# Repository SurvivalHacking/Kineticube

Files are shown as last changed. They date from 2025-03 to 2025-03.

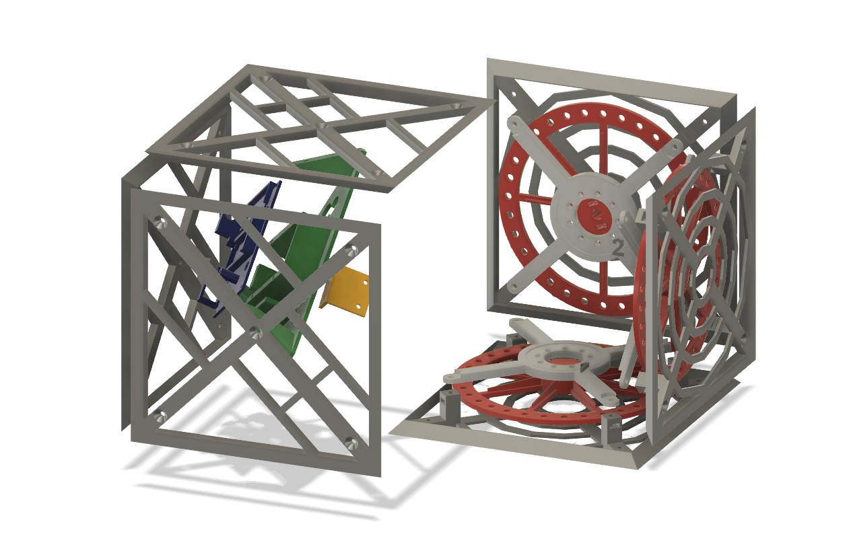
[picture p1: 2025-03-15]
Global Assembly.jpg

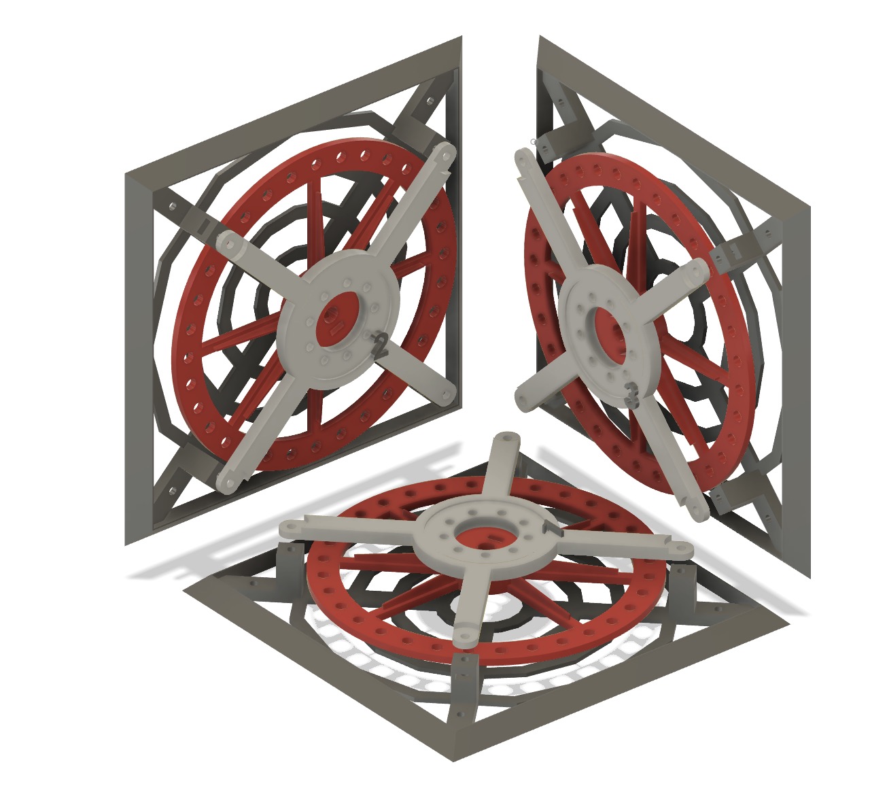
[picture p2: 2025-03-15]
Motor sequence.jpg

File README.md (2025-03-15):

Sometimes the futile things are always the most fascinating. 
Today I present the realisation of this self-balancing cube, nemed KinetiCube. 
An hypnotic cube that concentrates several scientific disciplines within it: Physics, mechanics, electronics and mathematics. 
As in an orchestra all working together in concert to make this cube stand upright.
Despite its simplicity, numerous operations and calculations are carried out in order to establish the right forces to be deployed. 
A beauty to look at and why not an opportunity to learn a few things from many angles. Sometimes even a simple game can become important for our growth. 
An open source project, which was, however, complex to realise and calibrate, so I put my own spin on it to make it feasible for everyone.

In addition I also made for a friend, the magician HYDE a version resembling a rubik's cube.
In this version, a number of improvements have been made to make it even simpler and aesthetically beautiful

Full video tutorial: https://youtu.be/8I2puoh9CxE 

EPXX-kineticube

COVER

Electronic assembly

Motor sequence

Global Assembly

Screenshot 2025-03-15 alle 20 30 26

Screenshot 2025-03-14 alle 22 32 57

Screenshot 2025-03-15 alle 20 29 16

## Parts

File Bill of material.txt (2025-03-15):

Tutorial video: https://youtu.be/8I2puoh9CxE

Bill of Material
🎛️ Nidec Motor 24H - ALI: https://s.click.aliexpress.com/e/_oEclh0V
🎛️ Digital Buzzer - ALI: https://s.click.aliexpress.com/e/_ooe48Gv
🎛 7mm Push Button - ALI: https://s.click.aliexpress.com/e/_Dnebs3t
🎛️ Power Switch 10x15 ALI: https://s.click.aliexpress.com/e/_DkAxjLh
🎛 Arduino Nano ALI: https://s.click.aliexpress.com/e/_DdZQhcR
🎛 Battery 11.1V 650mA - ALI: https://s.click.aliexpress.com/e/_omINxTT
🎛 XT30 battery cable - ALI: https://s.click.aliexpress.com/e/_ooCZeMv
🎛 Bluetooth Module HC05 - ALI: https://s.click.aliexpress.com/e/_oEKJG53

Original project:
https://github.com/remrc/Self-Balancing-Cube
https://hackaday.io/project/198415-arduino-3d-printed-self-balancing-cube

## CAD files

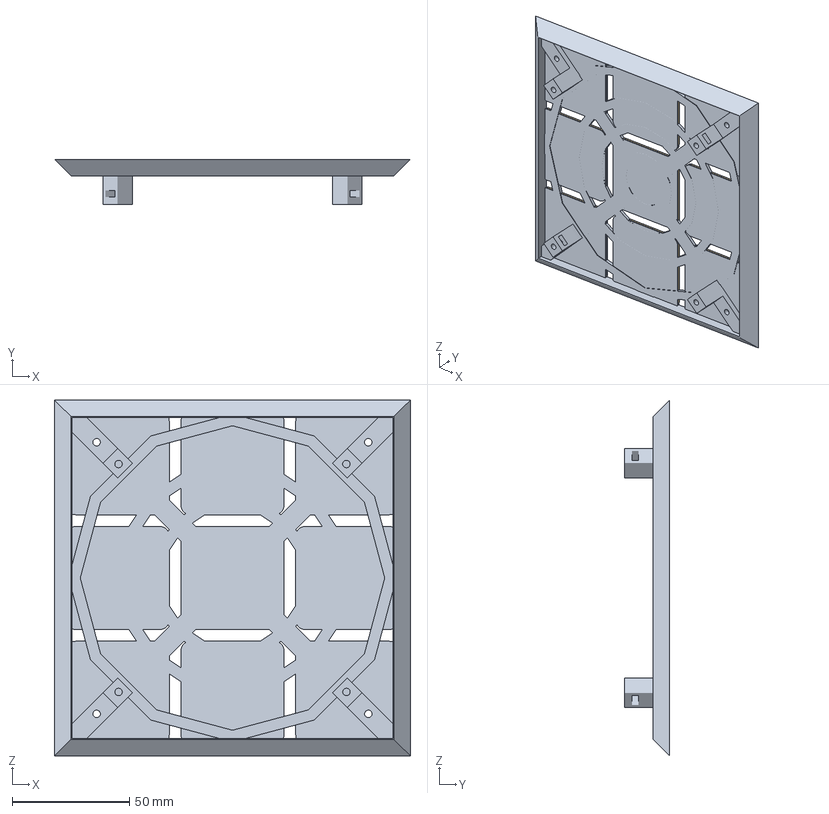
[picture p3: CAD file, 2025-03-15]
3D-HYDE/Motor Side.3mf
152.0 x 19.3 x 152.0 mm
Scheletro (4)
Sticker 1 (2) (2) (2) (2) (1) (1) (1)
Sticker 1 (2) (2) (2) (2) (1) (1) (2) (1)
Sticker 1 (2) (2) (2) (2) (1) (1) (2) (2)
Sticker 1 (2) (2) (2) (2) (1) (1) (2) (3)
Sticker 1 (2) (2) (2) (2) (1) (1) (2) (4)
Sticker 1 (2) (2) (2) (2) (1) (1) (2) (5)
Sticker 1 (2) (2) (2) (2) (1) (1) (2)
Sticker 1 (2) (2) (2) (2) (1) (1) (3)
Sticker 1 (2) (2) (2) (2) (1) (1)

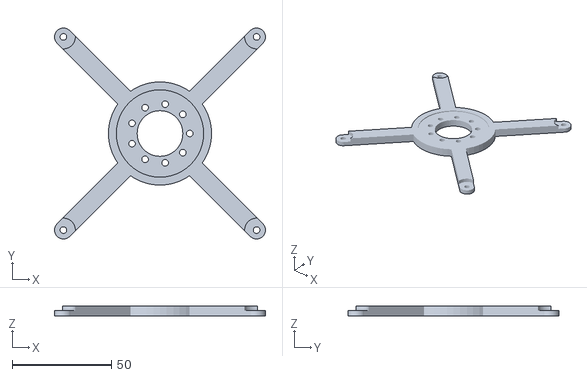
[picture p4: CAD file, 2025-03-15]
3D/Motor Support X3.stl
106.3 x 106.3 x 5.00

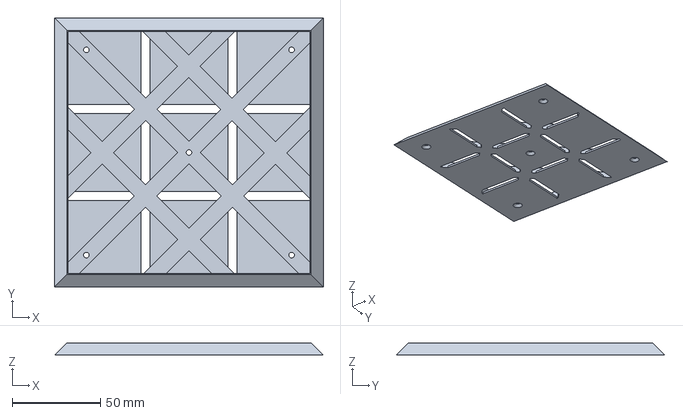
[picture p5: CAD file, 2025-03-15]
3D-HYDE/Normal side 2- BAMBULAB.3mf
152.0 x 152.0 x 7.00 mm

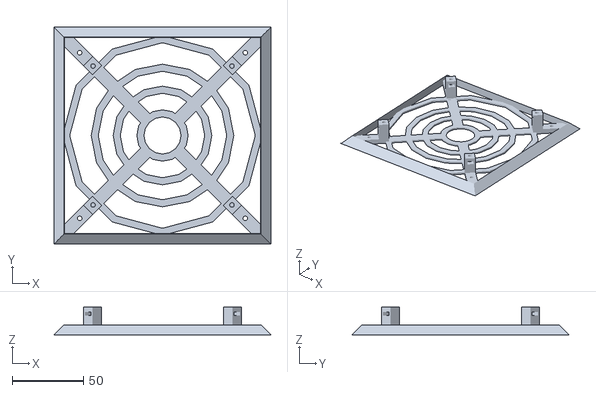
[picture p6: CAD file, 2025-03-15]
3D/Motor Side X3.stl
152.0 x 152.0 x 19.3

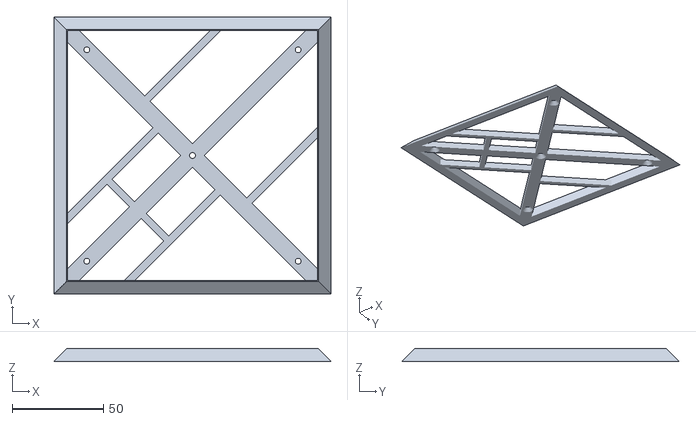
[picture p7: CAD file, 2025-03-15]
3D/Normal Side X3.stl
152.0 x 152.0 x 7.00

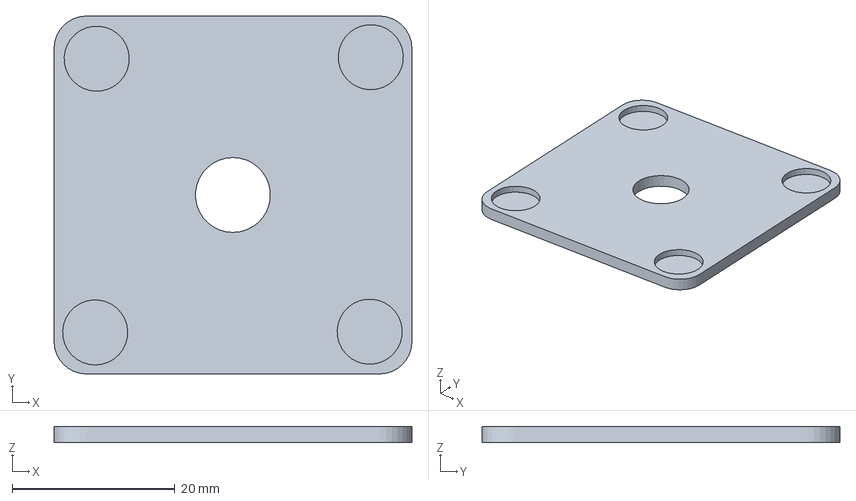
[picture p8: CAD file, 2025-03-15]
3D-HYDE/Magnet Sticker - BAMBULAB.3mf
44.0 x 44.0 x 2.00 mm

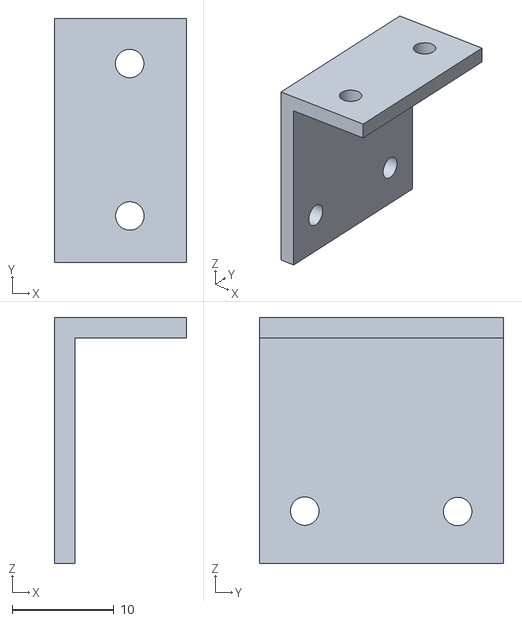
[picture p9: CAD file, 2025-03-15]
3D/Gyro Support.stl
13.0 x 24.1 x 24.2

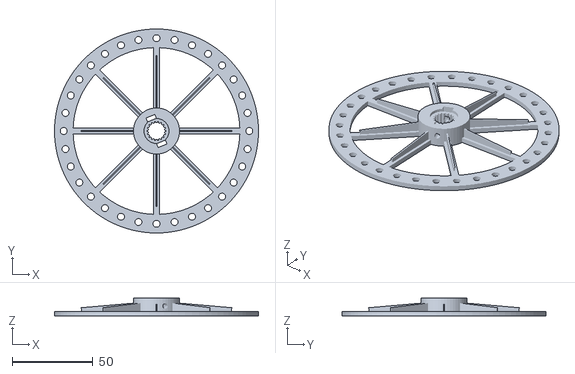
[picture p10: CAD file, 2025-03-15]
3D/Wheel 8mm hole X3.stl
126.4 x 126.4 x 11.0

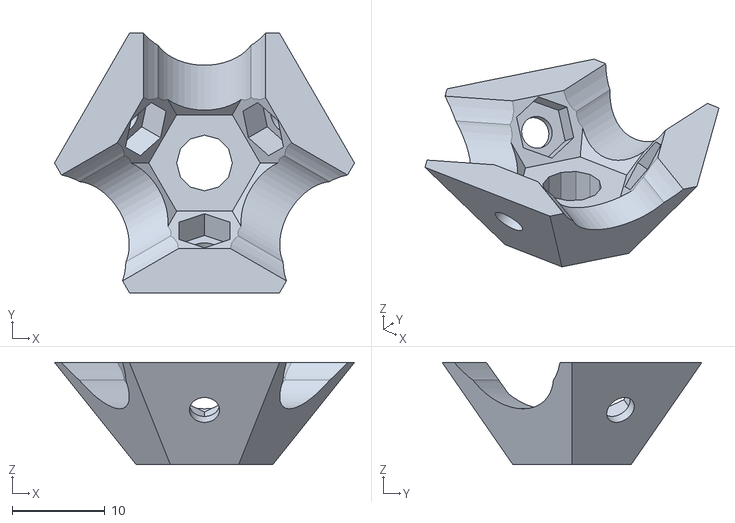
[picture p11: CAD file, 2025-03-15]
3D/Corners 8x.stl
32.3 x 28.0 x 11.0

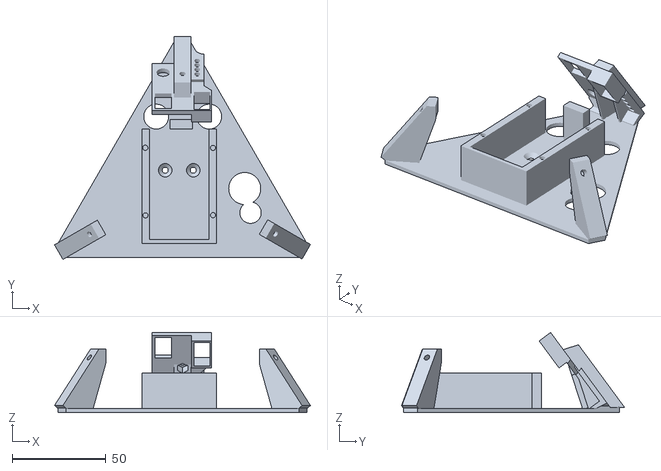
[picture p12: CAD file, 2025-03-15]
3D-HYDE/Electronic Support.stl
136.6 x 119.0 x 42.7

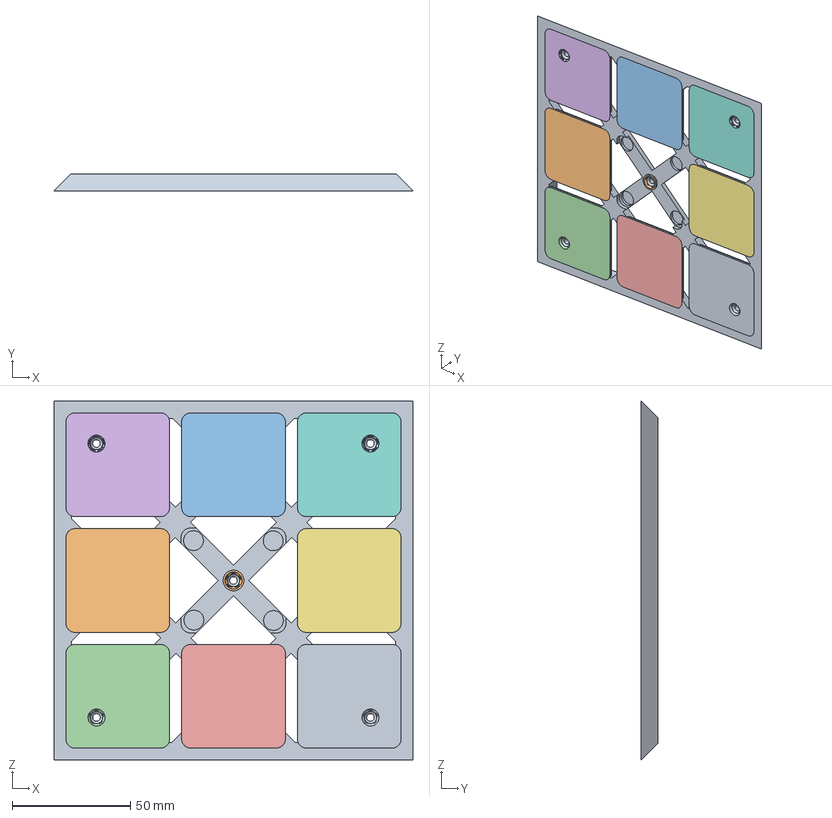
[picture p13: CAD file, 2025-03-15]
3D-HYDE/Normal Side magnet.3mf
152.0 x 7.00 x 152.0 mm
Scheletro (3) (1)
Sticker 1 (3) (3) (1) (1) (1)
Sticker 1 (3) (3) (1) (2) (1)
Sticker 1 (3) (3) (1) (3) (1)
Sticker 1 (3) (3) (1) (4) (1)
Sticker 1 (3) (3) (1) (5) (1)
Sticker 1 (3) (3) (1) (6) (1)
Sticker 1 (3) (3) (1) (7) (1)
Sticker 1 (3) (3) (1) (8)
Sticker 1 (3) (3) (2)

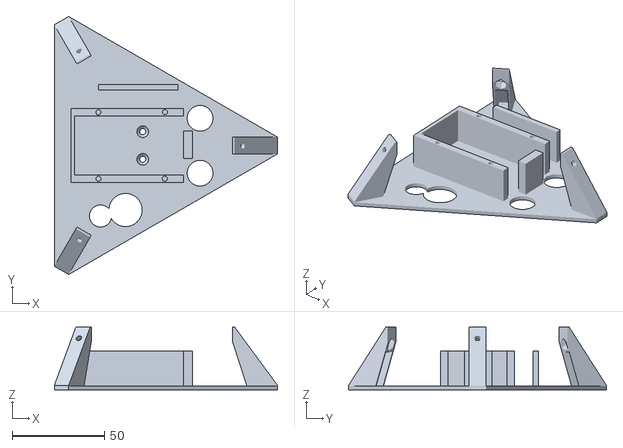
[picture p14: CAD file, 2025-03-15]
3D/Central Support.stl
121.2 x 139.9 x 34.1

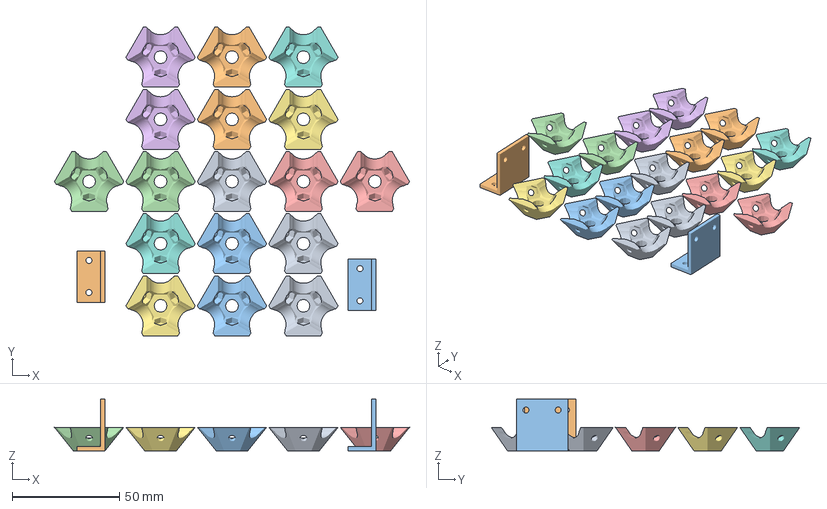
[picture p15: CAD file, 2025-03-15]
3D-HYDE/Internal and gyro FIX.3mf
165.6 x 143.9 x 24.2 mm
Corners 8x.stl x 17
Gyro Support.stl x 2

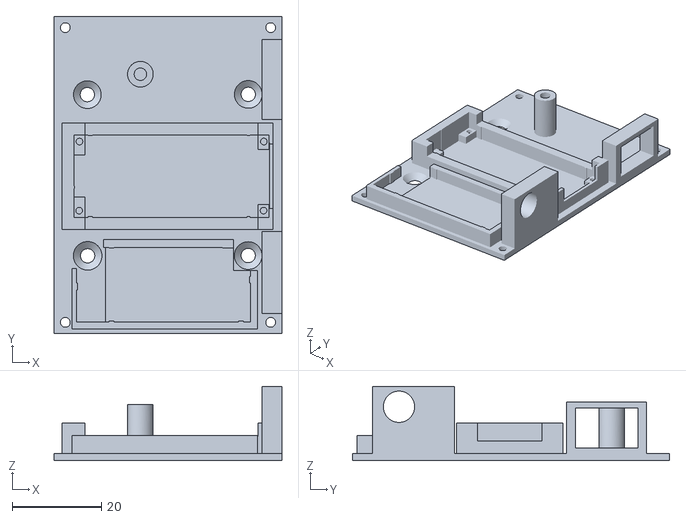
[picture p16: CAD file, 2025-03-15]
3D/Electronic Support.stl
51.0 x 71.0 x 16.6

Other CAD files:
3D-HYDE/Normal side 1- BAMBULAB.3mf
3D-HYDE/Motor Side 1- BAMBULAB.3mf
3D-HYDE/Normal Side.3mf
3D/Wheel 6mm hole X3.stl
3D-HYDE/Magnet sticker.3mf
3D-HYDE/Motor Side 2- BAMBULAB.3mf
3D-HYDE/Motor Support.3mf
3D-HYDE/Normal side 3 mgnet- BAMBULAB.3mf

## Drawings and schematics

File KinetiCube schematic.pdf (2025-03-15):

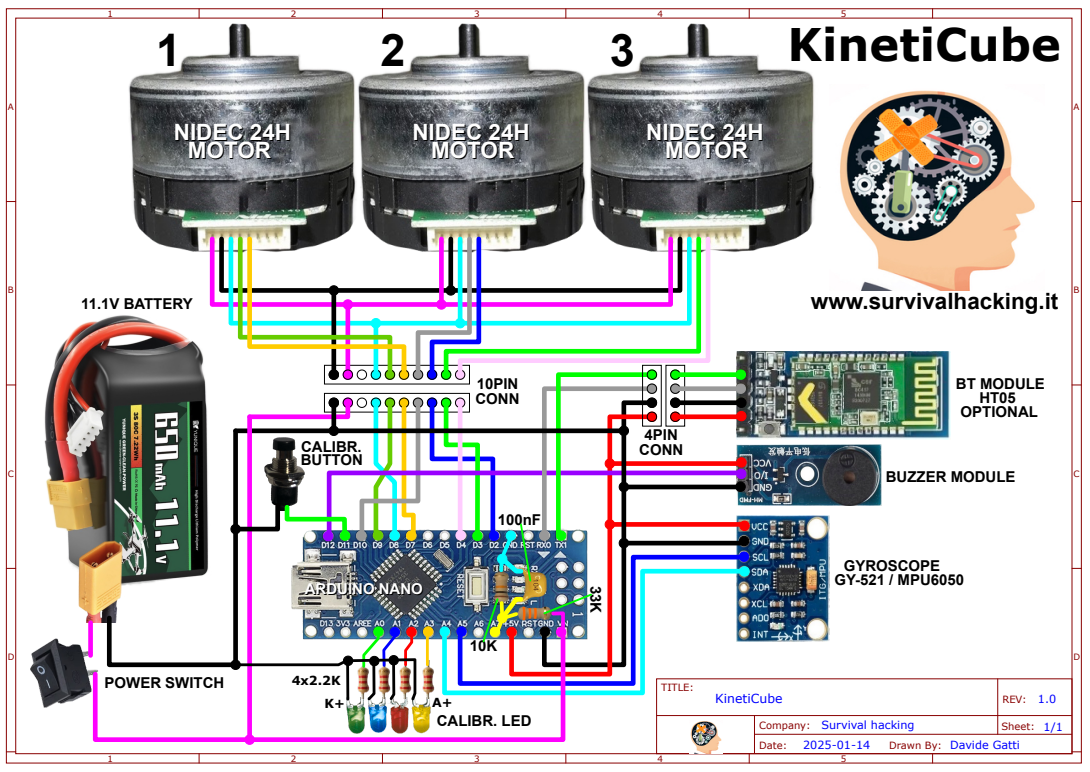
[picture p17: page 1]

CALIBR. BUTTON

TITLE:

KinetiCube | REV: 1.0

Company: Survival hacking | Sheet: 1/1

Drawn By: Davide Gatti

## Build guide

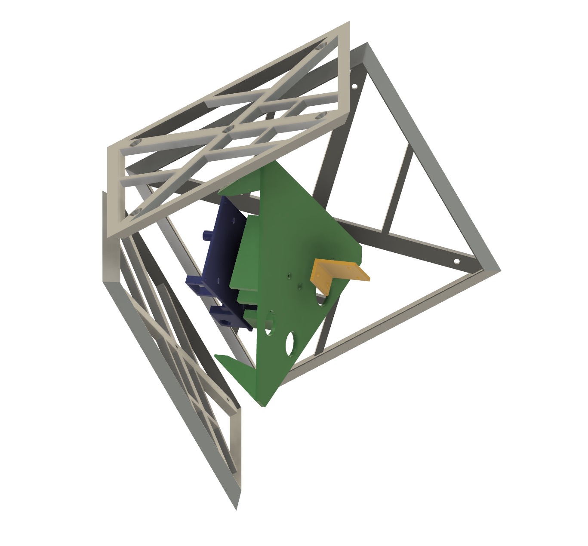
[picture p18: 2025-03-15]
Electronic assembly.jpg

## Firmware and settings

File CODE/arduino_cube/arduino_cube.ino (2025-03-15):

// Modified 20/01/2025 by Davide Gatti (www.survivalhacking.it) 
// Added manual calibration via pushbutton
// Added 4 LED for show calibration status

// Press  button to start calibration, press again to store calibration point (repeat the fo three edges and one angle
// If press button during power-up, forget current calibration


#include "arduino_cube.h"
#include <Wire.h>
#include <EEPROM.h>

void setup() {
  Serial.begin(115200);

  TCCR1A = 0b00000001;
  TCCR1B = 0b00001010;
  TCCR2B = 0b00000010;
  TCCR2A = 0b00000011;

  pinMode(DIR_1, OUTPUT);
  pinMode(DIR_2, OUTPUT);
  pinMode(DIR_3, OUTPUT);
  pinMode(BRAKE, OUTPUT);
  pinMode(BUZZER, OUTPUT);
  pinMode(CALIBRATE, INPUT_PULLUP);
  pinMode(LED_1, OUTPUT);
  pinMode(LED_2, OUTPUT);
  pinMode(LED_3, OUTPUT);
  pinMode(LED_4, OUTPUT);

  Motor1_control(0);
  Motor2_control(0);
  Motor3_control(0);
  if  (!digitalRead(CALIBRATE)) { // if press button during power on reset calibration
    save();
    beep();
    beep();
    beep();
  }
  
  EEPROM.get(0, offsets);
  if (offsets.ID1 == 99 && offsets.ID2 == 99 && offsets.ID3 == 99 && offsets.ID4 == 99) {
    calibrated = true;
  }else{
    calibrated = false;
  }
  
  Update_calibrated_LED();

  delay(3000);
  beep();
  angle_setup();
}

void loop() {

  currentT = millis();

  if (currentT - previousT_1 >= loop_time) {
    Tuning();  // derinimui
    angle_calc();
    
    if (balancing_point == 1) {
      angleX -= offsets.X1;
      angleY -= offsets.Y1;
      if (abs(angleX) > 8 || abs(angleY) > 8) vertical = false;
    } else if (balancing_point == 2) {
      angleX -= offsets.X2;
      angleY -= offsets.Y2;
      if (abs(angleY) > 6) vertical = false;
    } else if (balancing_point == 3) {
      angleX -= offsets.X3;
      angleY -= offsets.Y3;
      if (abs(angleY) > 6) vertical = false;
    } else if (balancing_point == 4) {
      angleX -= offsets.X4;
      angleY -= offsets.Y4;
      if (abs(angleX) > 6) vertical = false;
    }
 
    if (vertical && calibrated && !calibrating) {    
      digitalWrite(BRAKE, HIGH);
      gyroZ = GyZ / 131.0; // Convert to deg/s
      gyroY = GyY / 131.0; // Convert to deg/s

      gyroYfilt = alpha * gyroY + (1 - alpha) * gyroYfilt;
      gyroZfilt = alpha * gyroZ + (1 - alpha) * gyroZfilt;
      
      int pwm_X = constrain(pGain * angleX + iGain * gyroZfilt + sGain * motor_speed_pwmX, -255, 255); // LQR
      int pwm_Y = constrain(pGain * angleY + iGain * gyroYfilt + sGain * motor_speed_pwmY, -255, 255); // LQR
      motor_speed_pwmX += pwm_X; 
      motor_speed_pwmY += pwm_Y;
      
      if (balancing_point == 1) {
        XY_to_threeWay(-pwm_X, -pwm_Y);
      } else if (balancing_point == 2) {
        Motor1_control(-pwm_Y);
      } else if (balancing_point == 3) {
        Motor2_control(pwm_Y);
      } else if (balancing_point == 4) {
        Motor3_control(-pwm_X);
      }
    } else {
      balancing_point = 0;
      XY_to_threeWay(0, 0);
      digitalWrite(BRAKE, LOW);
      motor_speed_pwmX = 0;
      motor_speed_pwmY = 0;
    }
    previousT_1 = currentT;
  }
  
  if (currentT - previousT_2 >= 2000) {    
    battVoltage((double)analogRead(VBAT) / bat_divider); 
    if (!calibrated && !calibrating) {
      Serial.println("first you need to calibrate the balancing points...");
    }
    previousT_2 = currentT;
  }
}

void Update_calibrated_LED() {
  EEPROM.get(0, offsets);
  digitalWrite(LED_1, LOW);
  digitalWrite(LED_2, LOW);
  digitalWrite(LED_3, LOW);
  digitalWrite(LED_4, LOW);
  if (offsets.ID1 == 99) {
    digitalWrite(LED_1, HIGH);
  }
  if (offsets.ID2 == 99) {
    digitalWrite(LED_2, HIGH);
  }
  if (offsets.ID3 == 99) {
    digitalWrite(LED_3, HIGH);
  }
  if (offsets.ID4 == 99) {
    digitalWrite(LED_4, HIGH);
  }
}

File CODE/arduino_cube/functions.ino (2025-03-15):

void writeTo(byte device, byte address, byte value) {
  Wire.beginTransmission(device);
  Wire.write(address);
  Wire.write(value);
  Wire.endTransmission(true);
}

void beep() {
    digitalWrite(BUZZER, HIGH);
    delay(70);
    digitalWrite(BUZZER, LOW);
    delay(80);
}

void save() {
    EEPROM.put(0, offsets);
    EEPROM.get(0, offsets);
    if (offsets.ID1 == 99 && offsets.ID2 == 99 && offsets.ID3 == 99 && offsets.ID4 == 99) { 
      calibrated = true;
      tone(BUZZER, 1000, 500);
      tone(BUZZER, 2000, 500);
      tone(BUZZER, 3000, 500);
      tone(BUZZER, 4000, 500);
      tone(BUZZER, 5000, 500);
    }else{
      calibrating = false;
    }
    Update_calibrated_LED();
    Serial.println("calibrating off");
    beep();
}

void angle_setup() {
  Wire.begin();
  delay (100);
  writeTo(MPU6050, PWR_MGMT_1, 0);
  writeTo(MPU6050, ACCEL_CONFIG, accSens << 3); // Specifying output scaling of accelerometer
  writeTo(MPU6050, GYRO_CONFIG, gyroSens << 3); // Specifying output scaling of gyroscope
  delay (100);

  for (int i = 0; i < 1024; i++) {
    angle_calc();
    //Serial.println(GyZ);
    GyZ_offset_sum += GyZ;
    delay(3);
  }
  GyZ_offset = GyZ_offset_sum >> 10;
  Serial.print("GyZ offset value = "); Serial.println(GyZ_offset);
  beep();
  
  for (int i = 0; i < 1024; i++) {
    angle_calc();
    //Serial.println(GyY);
    GyY_offset_sum += GyY;
    delay(3);
  }
  GyY_offset = GyY_offset_sum >> 10;
  Serial.print("GyY offset value = "); Serial.println(GyY_offset);
  beep();
  beep();
}

void angle_calc() {
  
  // read raw accel/gyro measurements from device
  Wire.beginTransmission(MPU6050);
  Wire.write(0x45);
  Wire.endTransmission(false);
  Wire.requestFrom(MPU6050, 6, true);  
  GyY = Wire.read() << 8 | Wire.read(); // 0x45 (GYRO_YOUT_H) & 0x46 (GYRO_YOUT_L)
  GyZ = Wire.read() << 8 | Wire.read(); // 0x47 (GYRO_ZOUT_H) & 0x48 (GYRO_ZOUT_L)

  Wire.beginTransmission(MPU6050);
  Wire.write(0x3B);                  
  Wire.endTransmission(false);
  Wire.requestFrom(MPU6050, 6, true);  
  AcX = Wire.read() << 8 | Wire.read(); // 0x3B (ACCEL_XOUT_H) & 0x3C (ACCEL_XOUT_L)
  AcY = Wire.read() << 8 | Wire.read(); // 0x3D (ACCEL_YOUT_H) & 0x3E (ACCEL_YOUT_L)
  AcZ = Wire.read() << 8 | Wire.read(); // 0x3F (ACCEL_ZOUT_H) & 0x40 (ACCEL_ZOUT_L)

  GyZ -= GyZ_offset;
  GyY -= GyY_offset;

  robot_angleX += GyZ * loop_time / 1000 / 65.536;
  Acc_angleX = atan2(AcY, -AcX) * 57.2958;
  robot_angleX = robot_angleX * Gyro_amount + Acc_angleX * (1.0 - Gyro_amount);

  robot_angleY += GyY * loop_time / 1000 / 65.536;
  Acc_angleY = -atan2(AcZ, -AcX) * 57.2958; 
  robot_angleY = robot_angleY * Gyro_amount + Acc_angleY * (1.0 - Gyro_amount);

  angleX = robot_angleX;
  angleY = robot_angleY;

  if (abs(angleX - offsets.X1) < 0.4 && abs(angleY - offsets.Y1) < 0.4) {
    balancing_point = 1;
    if (!vertical) tone(BUZZER, 700, 500);;
    vertical = true;
  } else if (abs(angleX - offsets.X2) < 3 && abs(angleY - offsets.Y2) < 0.6) {
    balancing_point = 2;
    if (!vertical) tone(BUZZER, 900, 500);;
    vertical = true;
  } else if (abs(angleX - offsets.X3) < 6 && abs(angleY - offsets.Y3) < 0.6) {
    balancing_point = 3;
    if (!vertical) tone(BUZZER, 1100, 500);;
    vertical = true;
  } else if (abs(angleX - offsets.X4) < 0.6 && abs(angleY - offsets.Y4) < 3) {
    balancing_point = 4;
    if (!vertical) tone(BUZZER, 1200, 500);;
    vertical = true;
  }
}

void XY_to_threeWay(float pwm_X, float pwm_Y) {
  
  int16_t m1 = round(0.5 * pwm_X - 0.75 * pwm_Y); 
  int16_t m2 = round(0.5 * pwm_X + 0.75 * pwm_Y);
  int16_t m3 = pwm_X;  

  m1 = constrain(m1, -255, 255);
  m2 = constrain(m2, -255, 255);
  m3 = constrain(m3, -255, 255);
  
  Motor1_control(-m1); //-m1
  Motor2_control(-m2); //-m2
  Motor3_control(m3);  //m3
}

void battVoltage(double voltage) {
  //Serial.print("batt: "); Serial.println(voltage); //debug
  if (voltage > 8 && voltage <= 9.5) {
    digitalWrite(BUZZER, HIGH);
  } else {
    digitalWrite(BUZZER, LOW);
  }
}

void Motor1_control(int sp) {
  if (sp > 0) digitalWrite(DIR_1, LOW);
    else digitalWrite(DIR_1, HIGH);
  analogWrite(PWM_1, 255 - abs(sp));
}

void Motor2_control(int sp) {
  if (sp > 0) digitalWrite(DIR_2, LOW);
    else digitalWrite(DIR_2, HIGH);
  analogWrite(PWM_2, 255 - abs(sp));
}

void Motor3_control(int sp) {
  if (sp > 0) digitalWrite(DIR_3, LOW);
    else digitalWrite(DIR_3, HIGH);
  analogWrite(PWM_3, 255 - abs(sp));
}
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

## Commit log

2025-03-15 3D printer file for standard model
    [Central Support.stl, Corners 8x.stl, Electronic Support.stl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]
2025-03-15 Arduino sketch
2025-03-15 Practical assembly schematic
2025-03-15 Bill of Material
2025-03-15 Motor assembly sequence
2025-03-15 Electronic assembly sequence
2025-03-15 Global Assembly sequence
2025-03-15 3D printer file HYDE (rubik) edition
    [Electronic Support.stl, Internal and gyro FIX.3mf, Magnet Sticker - BAMBULAB.3mf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]
